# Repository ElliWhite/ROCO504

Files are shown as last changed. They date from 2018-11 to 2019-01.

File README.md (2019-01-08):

# ROCO504: Advanced Robot Design
## Active Robot Fall-Absorption Mechanism
### Mason Carter, Luka Danilovic, Elliott White

This is a repository to hold all the files for the ROCO504 project.

#### Requisites
The NUCLEO-F746ZG code needs to be loaded into https://os.mbed.com/ online compiler for it to work. 

mbed-os.lib revision 4928:e1bea44 also needs to be added to the project. 

### Project Assignment
For the assignment the group will need to design, implement and evaluate an advanced robot
design. Typical skills to be acquired/demonstrated include the use of CAD, FEA, 3D printing,
materials, mechanisms, robot programming and structural analysis. The project will enable the participents to
study, implement and test various aspects of robotics, including soft and exotic materials, novel
actuation principles, 3D-printable structures, and the interaction of a robot with its environment. 
A budget of £70 for the project is given.

### Abstract
The purpose of this research project was to design and build a prototype robot to serve as a proof of concept for a Active Robot Fall-Absorption Mechanism. Large robots with a small foot-base will inevitably fall over, so we have designed a mechanism to dampen the fall of a robot and reduce any damage caused to it from the fall. Upon successful completion of the building of the mechanism and conducting tests, our findings indicate that with slight improvements, originally not possible due to budget constraints, this project would yield a beneficial mechanism capable of performing its task of dampening a fall of a much larger robot.

### Introduction
As the trend of Robotics leans towards creating taller robots, more researchers are struggling with the task of trying to keep a robot with a small foot-base upright. The robot will, inevitably, fall over. This can cause massive damage to the robot, mostly consisting of mechanical damage to the links between joints, or servo damage. Until fall prevention becomes more effective, a simpler fall-damage-reduction system would be incredibly useful. 

We propose to design and create a robotic body and leg, for the provided budget of £70.00. The main body will consist of agonist-antagonist actuators and can detect when a robot has fallen past its self-balancing point. The leg will then reach out and use artificial tendons to reduce the falling speed of the body. This can be comparable to how a human might brace themselves when falling. The artificial tendons are used to store potential spring energy. 

### Design
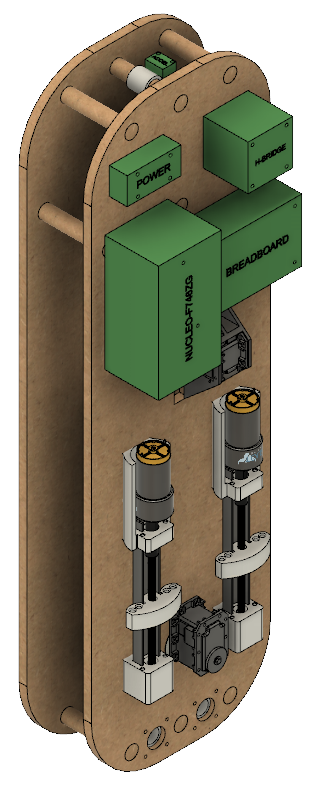
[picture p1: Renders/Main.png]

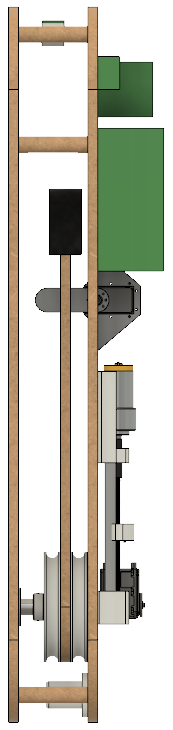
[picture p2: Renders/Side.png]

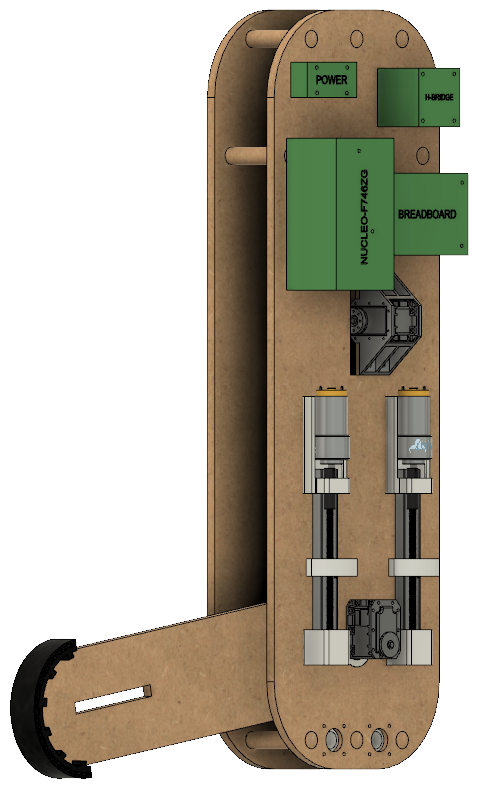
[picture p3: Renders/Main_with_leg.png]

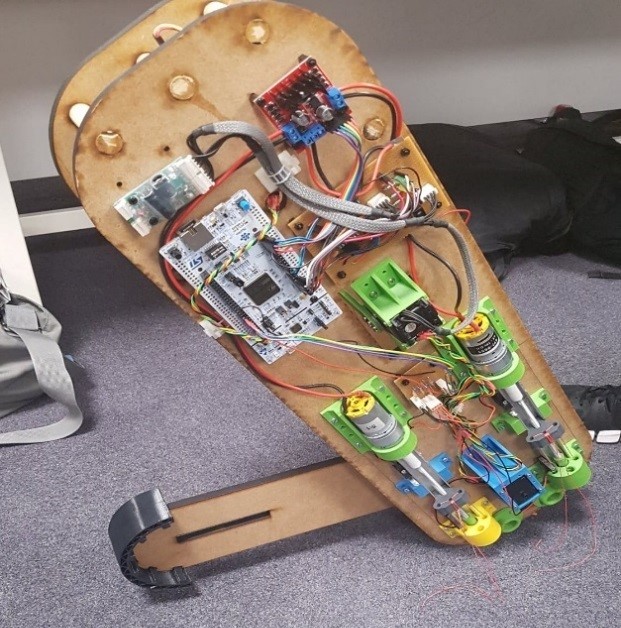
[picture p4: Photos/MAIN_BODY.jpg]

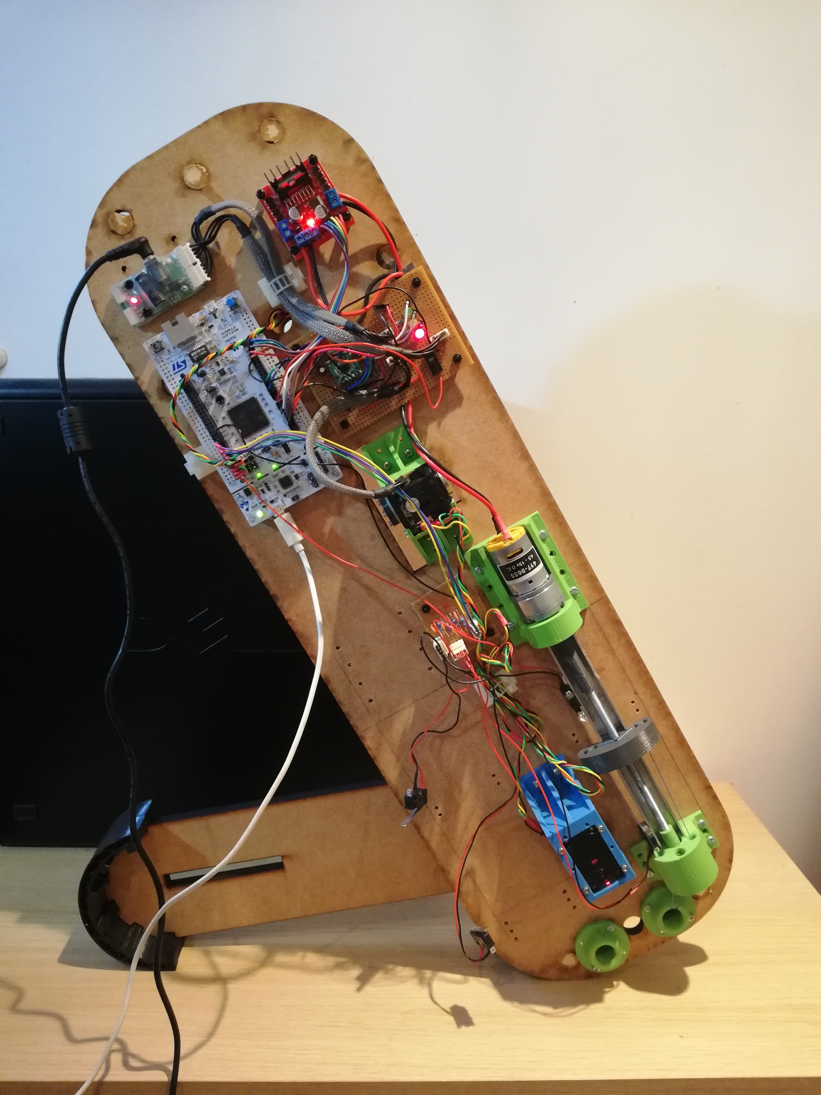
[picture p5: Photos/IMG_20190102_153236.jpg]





### Conclusion
Video: https://youtu.be/zlB8UxlkwFY

We have built a platform that, with more work, will be capable of demonstrating the use of agonist-antagonist joints and artificial soft tendons to absorb a fall of a robot. The software algorithms that are in place are capable of successfully executing a fall-reduction system, but it is the hardware that causes limitations. The motors do not have enough torque to slowly lower the body down to the floor, nor have a high enough RPM to tension the leg to a high enough degree before the body reaches the floor. 

The biggest improvement to be made would be changing the DC motors to a more powerful version. This would enable a faster actuation of the linear actuators and also allow the actuators to move when under heavy load and not stall. This change would also require a change to the motor driver IC to a part that would be able to handle the higher current.
A new pulley would have to be designed to stop the nylon-to-Fila-Flex adapter from slipping off during leg deployment. This would be a simple redesign and the modification that would need to be made would be to widen the pulley to the extent that there is no space between the pulley and the body for the adapter to fall into.

Another modification would be the leg pre-tensioning and release mechanism. The new control algorithm and mechanism would pre-tension both tendons at the same time regardless of which direction the body is falling. Then, upon detecting a fall, the mechanism would release one tendon and tighten the other one further. This would allow a quicker response time as there is no wait for one tendon to be tensioned and the other one un-tensioned during the time before a fall is detected.

The budget of £70 was a major limiting factor, and with a larger budget and with the previously-mentioned changes made, we believe the system would be successful in its ability to absorb the impact from a fall and not allow any damage to be caused to the robot it is attached to.

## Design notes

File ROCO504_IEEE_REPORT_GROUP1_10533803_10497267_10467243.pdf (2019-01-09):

# Active Robot Fall-Absorption Mechanism

Mason Carter
School of Computing, Electronics and Mathematics
University of Plymouth
Plymouth, UK
mason.carter@students.plymouth.ac.uk

Luka Danilović
School of Computing, Electronics and Mathematics
University of Plymouth
Plymouth, UK
luka.danilovic@students.plymouth.ac.uk

Elliott White
School of Computing, Electronics and Mathematics
University of Plymouth
Plymouth, UK
elliott.white@students.plymouth.ac.uk

Abstract – The purpose of this research project was to design and build a prototype robot to serve as a proof of concept for an Active Robot Fall-Absorption Mechanism. Large robots with a small foot-base will inevitably fall over, so we have designed a mechanism to dampen the fall of a robot and reduce any damage caused to it from the fall. Upon successful completion of the building of the mechanism and conducting tests, our findings indicate that with slight improvements, originally not possible due to budget constraints, this project would yield a beneficial mechanism capable of performing its task of dampening a fall of a much larger robot.

Keywords – Fall absorption, agonist-antagonist, variable stiffness, soft robot.

I. INTRODUCTION
As the trend of Robotics leans towards creating taller robots, more researchers are struggling with the task of trying to keep a robot with a small foot-base upright. The robot will, inevitably, fall over. This can cause massive damage to the robot, mostly consisting of mechanical damage to the links between joints, or servo damage. Until fall prevention becomes more effective, a simpler fall-damage-reduction system would be incredibly useful.

We propose to design and create a robotic body and leg, for the provided budget of £70.00. The main body will consist of agonist-antagonist actuators and can detect when a robot has fallen past its self-balancing point. A leg will then reach out and use artificial tendons to reduce the falling speed of the body. This can be comparable to how a human might brace themselves when falling. The artificial tendons are used to store potential spring energy.

II. DESIGN

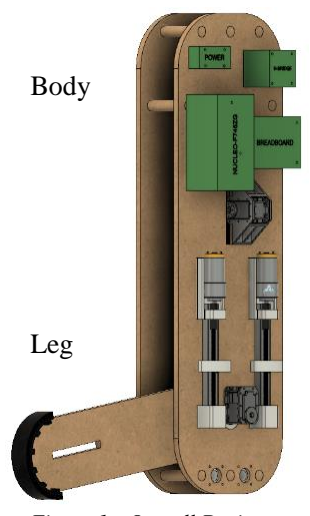
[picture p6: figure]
Body; Leg

Figure 1 - Overall Design

A. Mathematical Theory
Before the release of the leg, the falling motion of a robot is the same as that of an inverted pendulum. The model of an inverted pendulum and its corresponding equations [1] can be used to calculate the angular acceleration and thus the fall time of the robot. The calculations assume no friction or other resistance to movement, and any acceleration is due to gravity.
τ = mgl sin θ | (1)

τ = Iθ̈= ml

2 × θ̈ | (2)

ml

2θ̈= mgl sin θ | (3)

θ̈=

g
l
sin θ | (4)

t = √
(90 − θ)
θ̈
⁄ | (5)

Where:
- τ is the net torque around the pivot point.
- m is the mass of the body.
- g is the acceleration due to gravity.
- l is the length of the mass from the pivot point.
- θ is the angular displacement from the equilibrium.
- I is the moment of inertia of point mass.
- θ̈is the angular acceleration of the pendulum.
- t is the time to fall from the current angular displacement to perpendicular with the angle of equilibrium.

The time to fall can then be used to find the ‘activation window’, or the amount of time the leg will have to activate and contact the ground before the body is past its maximum angle. The maximum angle is an angle from the equilibrium that we feel the body could not be saved from with the use of the leg.

TA = √
(90 − θ1

)
θ̈
1

⁄ − √
(90 − θ2

)
θ̈
2
⁄ | (6)

Where TA is the activation window, θ1 is the current
angular displacement, θ2

is the maximum angle, θ̈
1

is the
angular acceleration for the current angular displacement, and θ̈
2

is the angular acceleration for the maximum angle.

With the calculation of the activation window, we can find the torque required to accelerate the leg quickly enough that it will contact the ground first.

θ̈
LEG =

θLEG
TA

2

(7)

θARM is the angle from its stored position (parallel to the body), and can be calculated using the following equation.

θLEG = θ − 90− sin⁻¹

l1 sin(90−θ)
l2

(8)

Where θ is the angular displacement of the body from equilibrium, l1
is the distance of the leg pivot to the base of the body, and l2
is the length of the leg.

Given the angular displacement, we can then calculate the angular acceleration required to activate and contact the ground in the activation window (Results for all cases in Appendix 1).

τLEG = mLEG × lLEG

2 × θ̈
LEG | (9)

Where τLEG is the torque around the leg’s pivot point, mLEG is the mass of the leg, lLEG is the distance of the legs centre of mass to the leg pivot point, and θ̈
LEG is the angular
acceleration of the leg required for the activation window.

As we can only make a rough estimation as to the dimensions of the body and leg, upper, middle and lower estimations were evaluated. 20° and 70° were chosen for the minimum and maximum activation angles. The torque required to activate by the maximum angle was calculated for each degree between the minimum and maximum angle, though not including the maximum.
This produced 50 results for each estimation, and with there being 5 unknown variables that can be estimated(l, l1 ,
l2

, lLEG, mLEG), the number of results quickly increases. To more quickly process and evaluate these results, a MATLAB script was written to carry out the calculations and output a ‘.csv’ file which can then be opened in Microsoft Excel. The variables were evaluated for values between 0.1 and 0.5, at intervals of 0.1. With the maximum angle set at 70°, we decided that the latest the leg should be able to activate would be at 45°, since the torque required for the leg to activate and contact the ground after 45° but before 70° would be incredibly large. Calculations showed that the torque required after this point could be up to 50000 Nm. With these variables, the minimum torque required would be 0.04 Nm and the maximum would be 93.7 Nm.

B. CAD and Mechanical Design
1) Design Overview
The body consist of two 9mm thick MDF, laser cut plates, (see Figure 1 for full CAD overview). The front plate, called the spine, serves as the attachment point for the PCBs, wiring, left and right tendon tensioning mechanisms, tendon guides, leg encoder Dynamixel servo, leg release

Dynamixel servo and the metal leg axle with bearing assembly. The Dynamixel servos were not included in the project budget as these were available for use when the project was undertaken. The second plate at the back serves to add depth to the body and provide additional structural support to the leg axle. This plate is attached to the spine via 7 dowels. The body has rounded corners at the bottom face so that area in contact with the ground will remain constant during the tipping of the body. Lighter components such as the PCBs have been mounted towards the top of the body with heavier components being pushed towards the base as much as the design permits. An accelerometer has been mounted at the top in line with the middle of the leg and oriented along the pivoting axis. (STL files for all components are available in Appendix 2).

2) Leg Design
The Leg consist of a single link as a multiple link configuration was found to be too complicated for a negligible improvement in performance. The leg can deploy along the tipping axis in forwards or backwards directions and is slightly raised from the base of the body to allow for deployment angle greater than 90o
. The base of the leg
contains a series of holes for attaching the tendons as well as two pullies of constant diameter around which the tendons wrap to ensure a constant force is exerted on the leg regardless of its orientation. The tendons are kept from tangling by using guide tubes to ensure alignment between the pulleys and the tensioning mechanism. The top of the leg is outfitted with a circular profile rubber “foot” to constantly provide same area of contact with the ground. Furthermore, the foot is 3D printed using NinjaFlex filament which creates a soft model. The foot also includes a self-resettable crumple zone to provide an additional element of compliance during a fall and to minimise the impact force of the leg. The leg also has positional feedback provided by the bottom Dynamixel (with gears removed to enable 360o
free rotation), while the leg release is controlled by a lever attached to a second Dynamixel positioned near the top of the leg. The whole leg is supported by a metal axle with bearings on both ends in the spine and back plate. This provides a stable axis of rotation and eliminates wobbling even in the cases of the hard impacts of the leg against the floor.

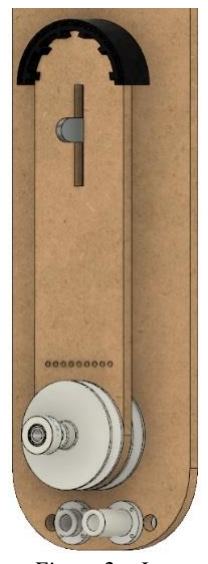
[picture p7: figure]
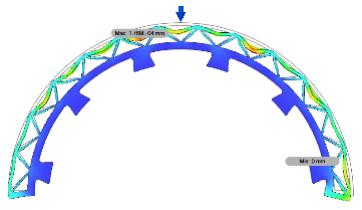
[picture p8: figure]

Figure 2 – Leg Figure 3 - Foot deformation under 500N Load

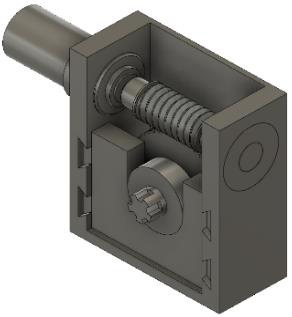
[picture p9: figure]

Figure 4 - Worm & Gear gearbox

3) Tensioning Mechanism Design
During the preliminary calculations phase, a goal was imposed on the tensioning mechanism so that it will be capable of 150mm of linear pull in 1 second. To achieve this a 12V DC motor was selected for its speed and torque. A 1974RPM (≈2000RPM) output was chosen for convenience with the highest torque option for the gearbox being selected at 1284gcm. To translate the motor rotation into linear movement of the tendons, a winding pulley was used with worm & gear gearbox (Figure 4) to make the tensioning mechanism non back-drivable. Therefore, the size of the pulley was calculated according to equation 10.

d =

60LN
πR

; {

d = Pulley Diameter
L = Linear Pull per Second N = Gear box ratio 1: N
R = RPM of tℎe Motor

(10)

After prototyping, it was determined that the best gearboxes worked with a ratio between 1:40 & 1:60. Therefore, number of teeth picked for the worm wheel is 48 to give a pulley diameter of 70mm. This in turn translates to a circumference of 220mm (>150mm). However, once the whole mechanism was assembled and run, there were friction problems which would cause failure of parts over prolonged use. Due to our budget constraints, we were unable to find a suitable prebuilt metal alternative and have therefore changed the design of the tensioning mechanism. Following the preliminary design review, a decision was taken to use a screw mechanism based on 3D printer Z-axis movement (Figure 5). A prototype was built, and a test was conducted to assess the viability of the mechanism. After a successful test, a full-scale device was built with support for 1.75mm and 2.5mm Fila-Flex tendon thickness. Minor

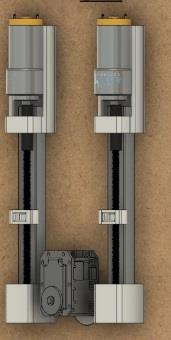
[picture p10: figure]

Figure 5 - Tensioning Mechanism Final Design

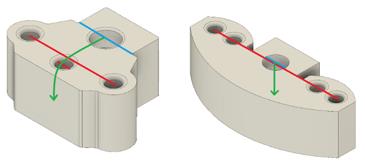
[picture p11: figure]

Figure 6 - Old and New Runners with respective Angular Moments

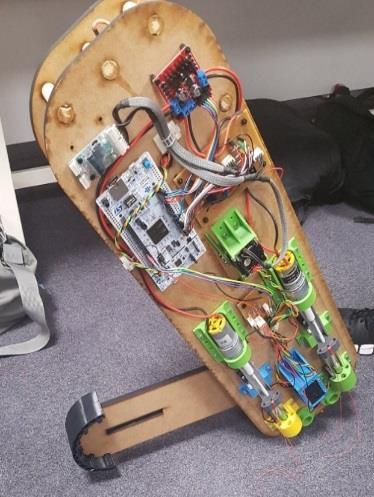
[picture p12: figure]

Figure 7 - Assembled Mechanism

changes were made to the shape of the tendon attachment points on the linear runner to reduce the angular moment on the runner and screw rod (see Figure 6) and therefore maximise the motor torque utilisation. This was done by aligning the mounting holes with the plane of the degree of freedom to achieve perpendicular force. The final design, when assembled, can be seen in Figure 7.

4) Tendon Design
The original tendon design was heavily inspired by the GummiArm [2]. Using a single strand of 2.85mm Fila-Flex and wrapping a string of nylon with ≈ 5mm spacing, we were able to test the tensioning mechanism but discovered that the strength of the nylon was not enough. Therefore, we switched to 1.75mm Fila-Flex and created a three-strand braid with 4th and 5th strands of nylon woven through. However, after conducting tensile testing on all configurations we realised that braid did not provide significant improvement over a straight three strand tendon, although it did add to the manufacturing complexity. To mitigate this, we switched back to a single strand of 2.85mm thick Fila-Flex. The final design that was chosen consists of double nylon strands connected to the runners on one end and via an adapter a strand of 2.85mm thick Fila-Flex on the other. Thicker filament was chosen for its strength and deformation properties. Fila-Flex then wraps around the

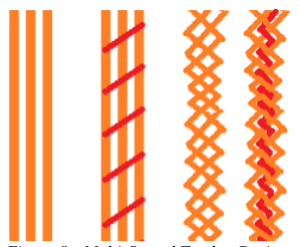
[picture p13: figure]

Figure 8 - Multi-Strand Tendon Designs pulleys and connects to the leg. As seen in Figure 9, there is a secondary nylon strand present in parallel with the Fila-Flex to take the force once the Fila-Flex is stretched passed the designated limit.

Figure 9 – Compound Tendon Diagram

C. Electronics & Software Design
The whole system is built around a STM32F746ZG MCU which sits upon a NUCLEO-F746ZG development board, produced by STMicroelectronics. The motor driver selected is a Dual H-Bridge Module produced by Hobby Components, which contains a L298N produced by STMicroelectronics. The L298N can provide up to 2A continuous per channel, or 2.5A repetitive (80% on, -20% off). This motor driver module is connected to two RS PRO brushed DC geared motor. These DC motors have a stall current of 2.26A. The L298N can handle the stall current of these motors, but it should be noted that if other, more powerful motors were to be used, then a different motor driver would need to be chosen. The six-axis inertial measurement unit selected is an inexpensive MPU-6050, produced by TDK InvenSense, and comprises of a gyroscope and an accelerometer. This IMU sits on a breakout board produced by SODIAL, the GY-521. Communication to the sensor is achieved through I2C. Dynamixel servos have been used in the design. The two Dynamixel servos are RX-28s, and these require the RS-485 communication protocol. Because of this, a MAX3088 RS-485 transceiver IC has been used in line with a MAX3378 voltage-level shifter and are connected to a UART port on the NUCLEO board with a baud rate of 57600. The servos can be connected in a daisy chain-like manner. Microswitches have been used on the linear actuators to provide positional feedback of the linear runners when they reach their limit. LEDs have also been used for visual debugging and system information. An outline of the system can be seen in Figure 10.

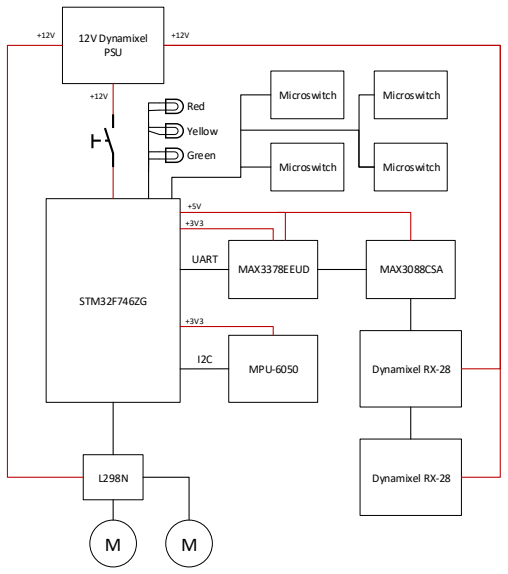
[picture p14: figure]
STM32F746ZG; 12V Dynamixel PSU; MPU-6050; Dynamixel RX-28; Red; Green; Yellow; MAX3378EEUD; MAX3088CSA; Microswitch; UART

Figure 10 - Electronics System Outline

One of the Dynamixel RX-28s has been used as an encoder to provide positional feedback of the leg. To achieve this, the gears have been removed so the servo is free to spin. Communications between the RX-28s and the NUCLEO board occur by sending and receiving digital packets. A library on Mbed had been provided [3] to enable communications with the servos. However, this library had to be modified to get it working with the RX-28s. Timings in the existing library had been incorrect, so the microcontroller would completely miss the returning status packet from the servos. If the microcontroller tried to communicate with a servo that wasn’t in the servo chain, then the code would enter an infinite wait. This has been changed to include a timeout if a status packet isn’t received within 5000 checks of the serial input buffer. A new function had been implemented to find the servo ID numbers of the servos in the servo chain. This means that the servos could be switched out with other RX-28s, and the code would still work. The baud rates of the Dynamixel servos can be changed by modifying data in the registers on the on-board EEPROM. Because of this, some of the servos had different baud rates to each other at the start of the project. An algorithm was implemented to quickly adjust the baud rates of the servos in the chain by utilising the “broadcast” command, which sends an instruction to all the servos on the chain. This algorithm ensured that all servos in the chain had the same baud rate before the rest of the code ran. Tests were done to identify the servos in the chain and to move the servos to different positions. Reading back the positional data was also done to ensure that the communications with the servos were established correctly.

To test and use the MPU-6050, an existing header and main file had been used that was provided on Mbed [4]. These files provided all the functionality to read acceleration and angular data. The algorithm uses Quaternions to avoid gimble lock in the gyroscope. This is especially useful in this scenario as the robot will approach +/- 90 degrees in one axis. The Quaternions are then converted to Euler angles using the conversion equations 11-13.
φ (yaw) = arctan (

2(ab+cd)
a²−b

2−c

2−d²

| | | | ) | | (11)
θ (pitcℎ) = −arcsin(2(bd − ac)) | (12)

ψ (roll) = arctan (

2(ad+bc)
| | | a²+b 2−c | 2−d²
| | | | ) | | (13)

To test the IMU, continual data was streamed to a serial monitor to observe the angular data of the device. The device was then rotated around its separate axis and the measured data was compared to the real angles of the device.

All the software has been written in C++ using ARM’s Mbed OS, which is a platform and operating system for
devices | based | on | the | 32-bit | ARM | Cortex-M
microcontrollers. This has enabled rapid code development and fast deployment. The algorithms used focus heavily on gyroscopic and accelerometer data as it is this data that

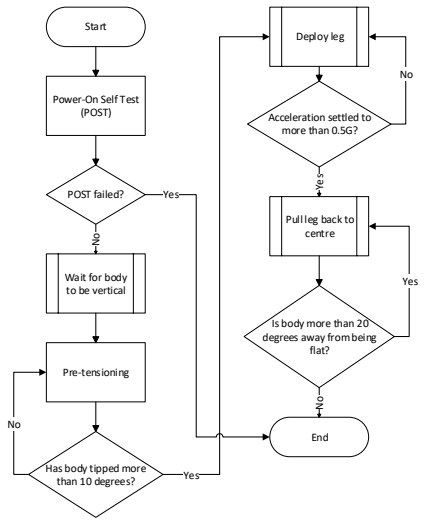
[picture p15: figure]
Start; Power-On Self Test (POST); POST failed?; Wait for body to be vertical; Pre-tensioning; Has body tipped more than 10 degrees?; Acceleration settled to more than 0.5G?; Deploy leg; Pull leg back to centre; Is body more than 20 degrees away from being flat?; End; No Yes; Yes

Figure 11 - Code Algorithm Outline

provides all the information about the given state of the body. Data from the IMU is gathered asynchronously as it is not critical to observe the physical state of the body at a given rate. An outline of the algorithm used for this project can be seen in Figure 11.
As seen in Figure 11, the algorithm begins by running a POST test. This ensures that all components are working and that communications with the Dynamixels are established. The pre-tensioning function tensions the tendons on the leg before the body has begun to fall. This is done by detecting which direction the body is starting to tip, and subsequently pull on the relevant tendons. If the body is tipped more than 10 degrees, this is classed as a ‘fall’ and the leg is deployed in the correct direction. The acceleration data is then monitored until it settles. This shows that the body has stopped falling and is resting on the leg. The leg is then pulled back towards the centre of the body using positional data from the Dynamixel on the shaft of the leg to monitor its progress.

III. EXPERIMENTS

A. Tensile Testing
In order to pretension the agonist-antagonist joints, an elastic material would be used as a tendon. The kinetic energy from the pre-tensioning would be stored in the tendon to be released as needed. Flexible 3D printing filament (FilaFlex [5]) would be used, both because of cost and its elasticity at break of 665%.
Three strands of the filament would be used, because the pre-tensioning forces had been estimated to be too much for a single strand, and to also provide a built in redundancy in the case of a strand snapping. As with rope, it was thought that the tensile strength of the material could be increased by braiding the strands, so test samples were produced for both un-braided and braided. However, while an elastic material is needed, the elasticity of the filament seemed too high, so a compound tendon using Nylon was considered. Test samples for unbraided with nylon and braided with nylon were also produced for tensile testing. Two test samples for each configuration of the strands were tested for their tensile strength, but because of inadequate clamping

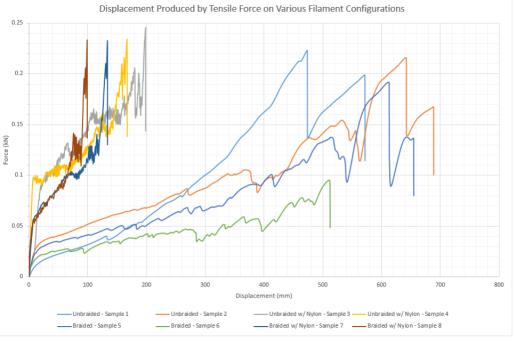
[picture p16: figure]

Figure 12 - Copy of the Tensile Testing Results Graph

methods the samples tended to slip through the clamping mechanism. Appendix 3 contains the results of the testing. The graph in Figure 12 and in Appendix 3 shows that while the samples with and without Nylon are clearly separated, braiding has no effect on the tensile strength of the material.

B. Fall Testing
In order to be able to correctly use the accelerometer and gyroscopic data, the body needed to be repeatedly pushed over and the data recorded. This allowed the system to know the state of the body based on the data. The tendons were configured in a way that would allow the body to rest at an angle with all the weight resting on the tendon. The right motor was spun until the linear actuator had pulled a substantial amount on the tendon. This can be seen in Figure
13. The body was then up-righted and pushed over with a small amount of force. The acceleration in the x-axis was monitored and plotted through a serial connection to a MatLab script. This plot can be seen in Figure 14. At sample 150, the body starts to fall. At 380, the Fila-Flex starts to dampen the fall and slow the body down, and at sample 420 the nylon takes over which causes the large jump in acceleration. As the body settles to its resting position, so does the acceleration which settles at 0.9G. It does not settle at 0G as the accelerometer is measuring the acceleration due to Earth’s gravity. Initially, a value of 0 will be measured, but as the body tips over more, the value will increase until it reaches 1G when the body is perpendicular to the floor. This data has helped shape the control algorithm (Appendix 4). If the acceleration has settled to a high value, then it can be known that the body has stopped moving and is resting on the leg. The leg can then start to be pulled back towards the body and lower the body down towards the ground. It was decided that if the acceleration settles to a value above 0.5G, then the body has successfully fallen and is resting on the leg (Appendix 5 - Video).

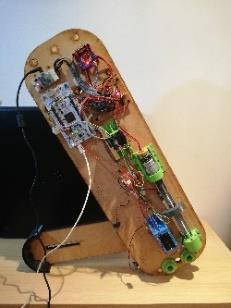
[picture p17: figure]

Figure 13 - Body Resting on Leg

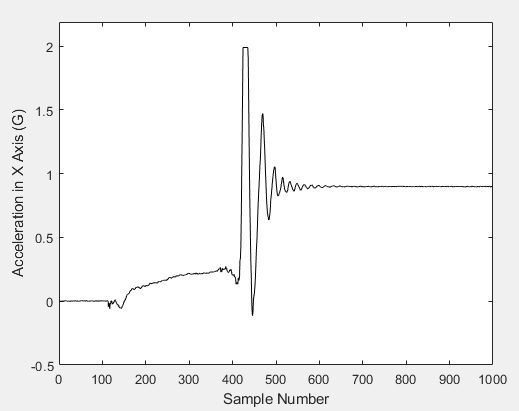
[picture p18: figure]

Figure 14 - Graph Showing Change in Acceleration in X-Axis

C. Lowering Body Testing
The next experiment was testing to see if the body could be lowered slowly to the ground once it had rested on the leg. The body was placed at an angle with all of the strain on the tendons, and then the right motor was spun in such a way that would pull the leg into the body and allow the body to reach the floor. It was found that the motor would stall and not have enough torque to move the linear actuator. The body would not be able to be lowered down to the floor. The force of the tendons pulling on the linear runner was causing too much friction between the nut and the threaded rod, stopping the motor from spinning.
D. General Testing
Once the body was built there was a lot of general testing of tipping the body and pushing it over, and then observing how the control algorithm was performing. During this testing, it was found that the tendons would never tension enough when the body was falling. The RPM of the motors were not high enough to move the linear actuator far enough in the time given for the body to fall over.
We also found that when the leg sprung out and the body tipped, the tendon would become displaced from the pulley (see Figure 15). This resulted in a much looser tendon as it was not stretched around the pulley. This, coupled with the fact that linear actuator would not move far enough, meant that the tendon would never be taught enough to have any effect on dampening the fall of the body.

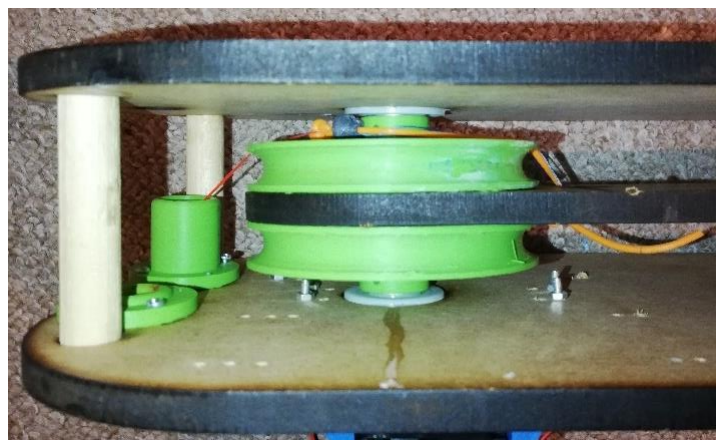
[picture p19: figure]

Figure 15 - Tendon Slipped off Pulley

IV. CONCLUSION
We have built a platform that, with more work, will be capable of demonstrating the use of agonist-antagonist joints and artificial soft tendons to absorb a fall of a robot. The software algorithms that are in place are capable of successfully executing a fall-reduction system, but it is the hardware that causes limitations. The motors do not have enough torque to slowly lower the body down to the floor, nor have a high enough RPM to tension the leg to a high enough degree before the body reaches the floor. The biggest improvement to be made would be changing the DC motors to a more powerful version. This would enable a faster actuation of the linear actuators and allow the actuators to move when under heavy load and not stall. This change would also require a change to the motor driver IC to a part that would be able to handle the higher current. A new pulley would have to be designed to stop the nylon-to-Fila-Flex adapter from slipping off during leg deployment. This would be a simple redesign and the modification that would need to be made would be to widen the pulley to the extent that there is no space between the pulley and the body for the adapter to fall into. Another modification would be the leg pre-tensioning and release mechanism. The new control algorithm and mechanism would pre-tension both tendons at the same time regardless of which direction the body is falling. Then, upon detecting a fall, the mechanism would release one tendon and tighten the other one further. This would allow a quicker response time as there is no wait for one tendon to be tensioned and the other one un-tensioned during the time before a fall is detected. The budget of £70.00 was a major limiting factor, and with a larger budget and with the previously-mentioned changes made, we believe the system would be successful in its ability to absorb the impact from a fall and not allow any damage to be caused to the robot it is attached to.

APPENDIX
Appendix 1 – Force Calculations https://github.com/ElliWhite/ROCO504/tree/master/Force %20Calculations (https://github.com/ElliWhite/ROCO504/tree/master/Force%20Calculations)

Appendix 2- STL Files
https://github.com/ElliWhite/ROCO504-Advanced-Robot-Design-Project/tree/master/STL%20Files (https://github.com/ElliWhite/ROCO504-Advanced-Robot-Design-Project/tree/master/STL%20Files)

Appendix 3 – Tensile Testing Data and Results
(Graph available in “Displacement vs. Force” worksheet). https://liveplymouthac-my.sharepoint.com/:x:/r/personal/elliott_white_students_plymouth_ac_uk/_layouts/15/Doc.aspx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 56e5c-52d3-4ef5-bb82-
3eb3c2f34c49%7D&action=default (https://liveplymouthac-my.sharepoint.com/:x:/r/personal/elliott_white_students_plymouth_ac_uk/_layouts/15/Doc.aspx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)

Appendix 4 – GitHub Repository
(ReadMe available) https://github.com/ROCO504/2018-Group1 (https://github.com/ROCO504/2018-Group1)
Populated repository can be found at: https://github.com/elliwhite/roco504

Appendix 5 – Video demonstrating the Project https://youtu.be/zlB8UxlkwFY

ACKNOWLEDGMENT
This research was supported by Martin Stoelen from the University of Plymouth CRNS. We thank our colleagues from University of Plymouth Robotics Department who provided insight and expertise that greatly assisted the research, although they may not agree with all of the interpretations/conclusions of this paper.
V. REFERENCES
[1] Wikipedia, “Inverted Pendulum,” 15 June 2018.
[Online]. | Available:
https://en.wikipedia.org/wiki/Inverted_pendulum. [Accessed October 2018].
[2] M. Stoelen, “GummiArm,” 2017. [Online]. Available: https://mstoelen.github.io/GummiArm/. [Accessed November 2018].
[3] D. Gongora, “Dynamixel,” 25 October 2015.
[Online]. | Available:
https://os.mbed.com/users/dmgongora/code/Dynamixel/. [Accessed October 2018].
[4] K. Winer, “MPU6050IMU,” 29 June 2014.
[Online]. | Available:
https://os.mbed.com/users/onehorse/code/MPU6050IMU/.
[5] | Recreus, | “FilaFlex | Original | 82A,” | 2017.
[Online]. | Available:
https://recreus.com/img/pdf/FILAFLEX%2082A%20TECHNICAL%20SHEET%20&%20MSDS%2 02017.pdf. [Accessed October 2018].

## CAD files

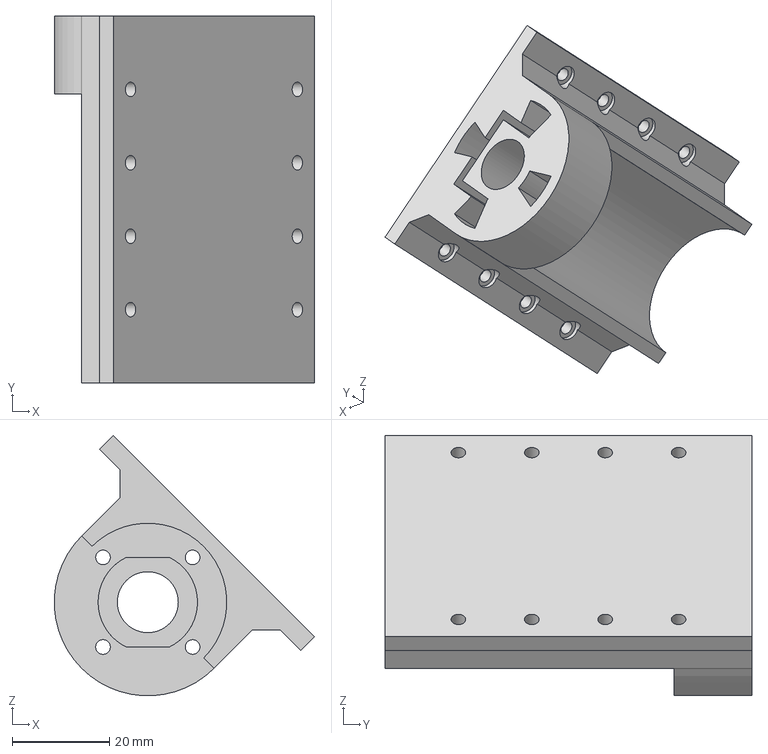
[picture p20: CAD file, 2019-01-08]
STEP Files/Motor Mount v5.step
53.4 x 75.3 x 53.4 mm

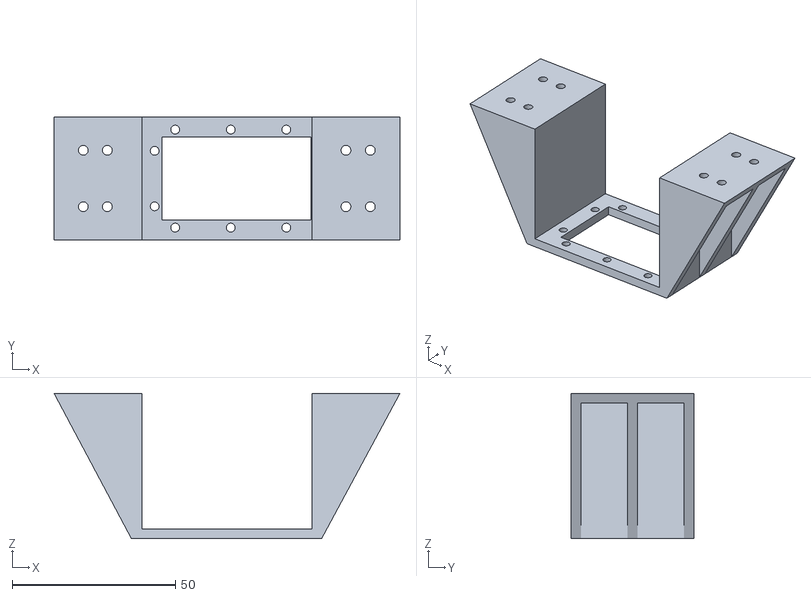
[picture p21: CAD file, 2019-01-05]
STL Files/Bottom Dynamixel Bracket v5.stl
105.9 x 37.5 x 44.5

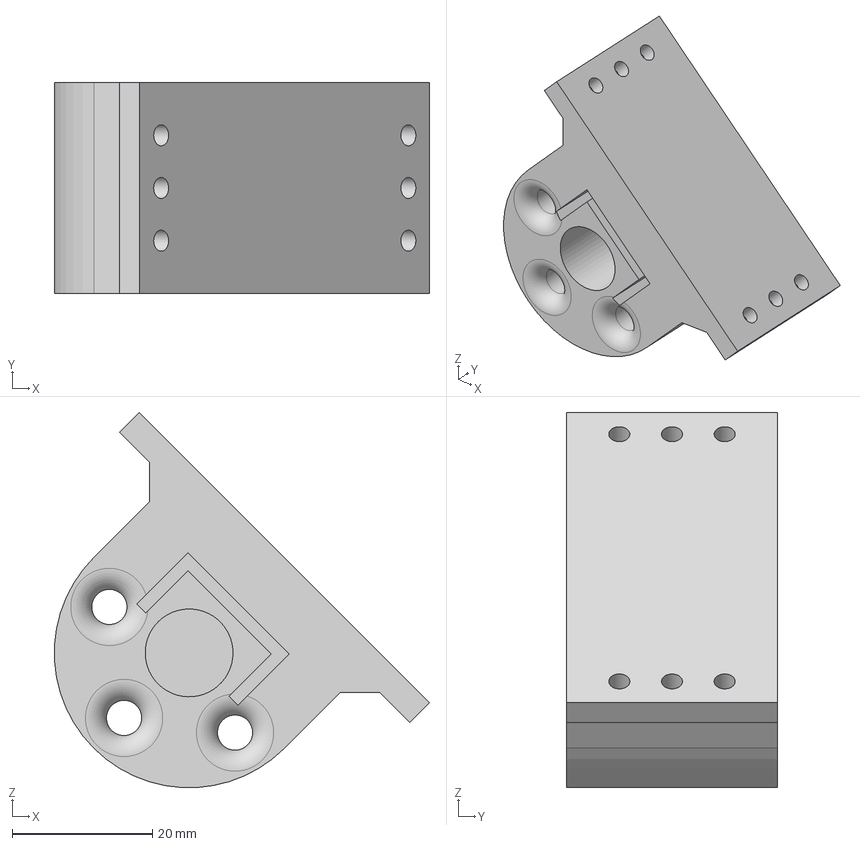
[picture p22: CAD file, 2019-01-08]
STEP Files/Runner End v5.step
53.4 x 30.0 x 53.4 mm

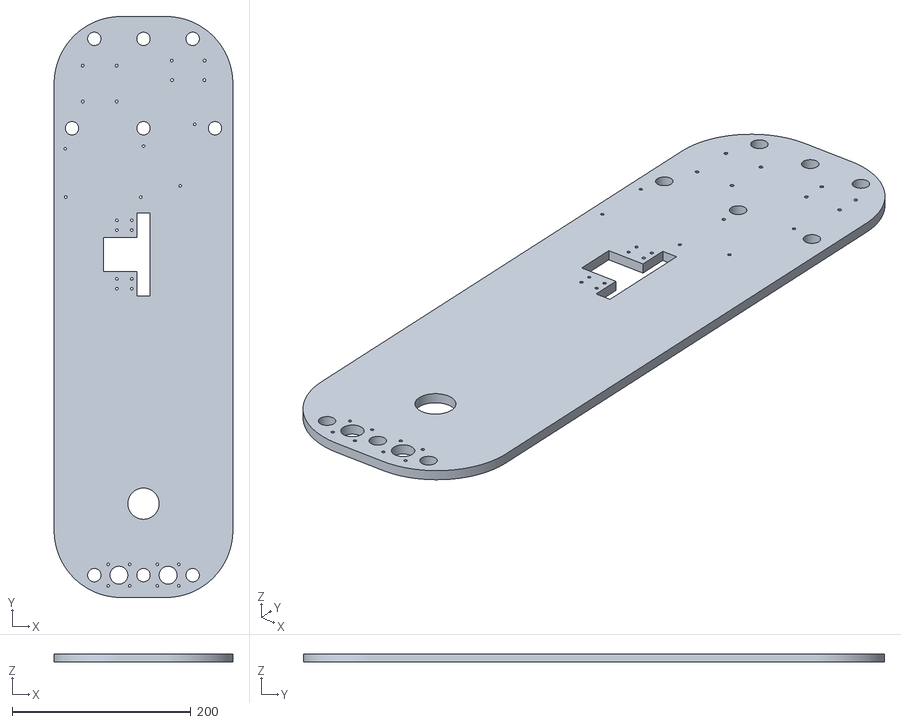
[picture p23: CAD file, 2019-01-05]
STL Files/Spine v6.stl
200.0 x 650.0 x 9.00

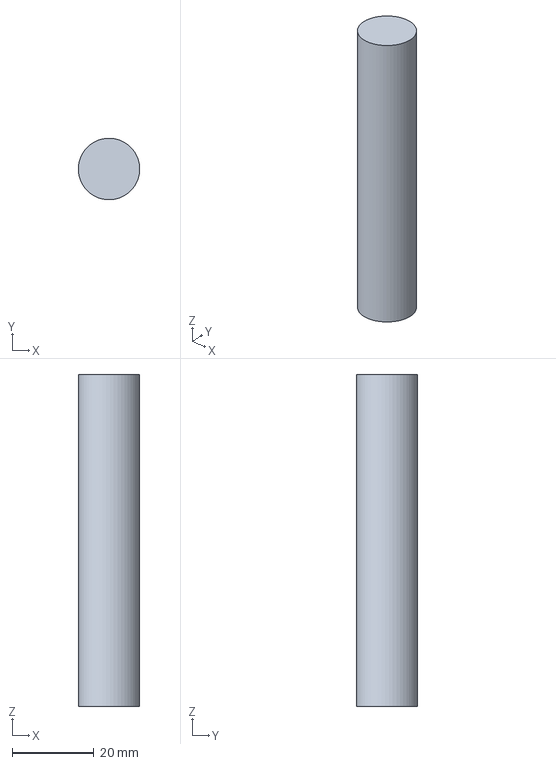
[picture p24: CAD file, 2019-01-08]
STEP Files/Dowel v11.step
15.0 x 15.0 x 81.0 mm

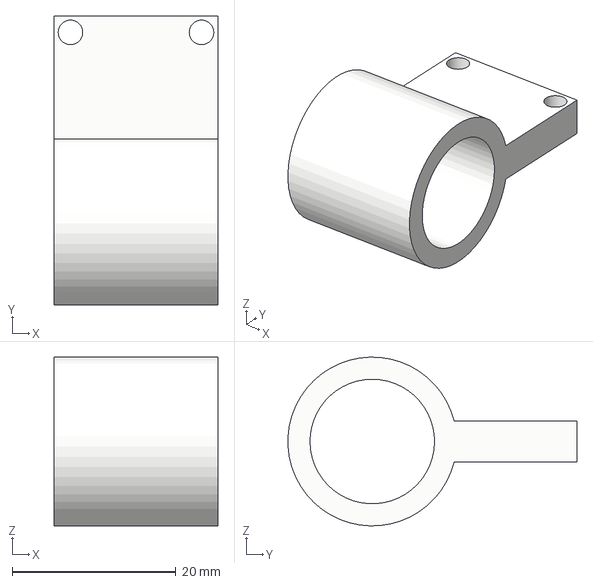
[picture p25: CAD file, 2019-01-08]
STEP Files/Acc Bracket v1.step
20.0 x 35.3 x 20.6 mm

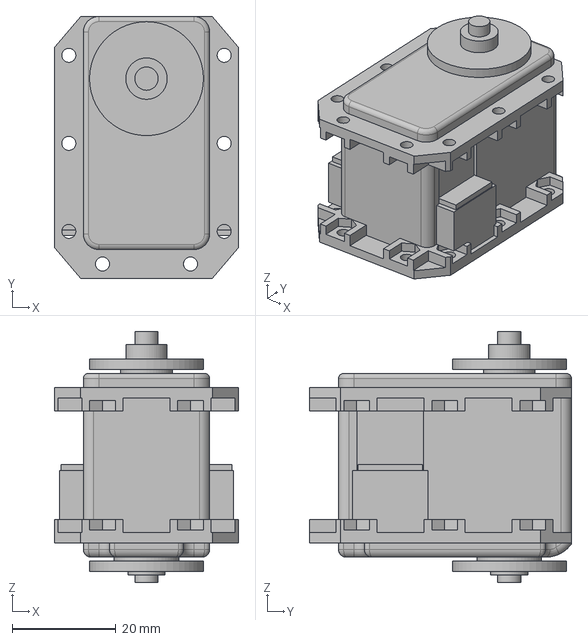
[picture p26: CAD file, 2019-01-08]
STEP Files/Dynamixel RX28 Representation v1.step
35.6 x 50.6 x 48.5 mm

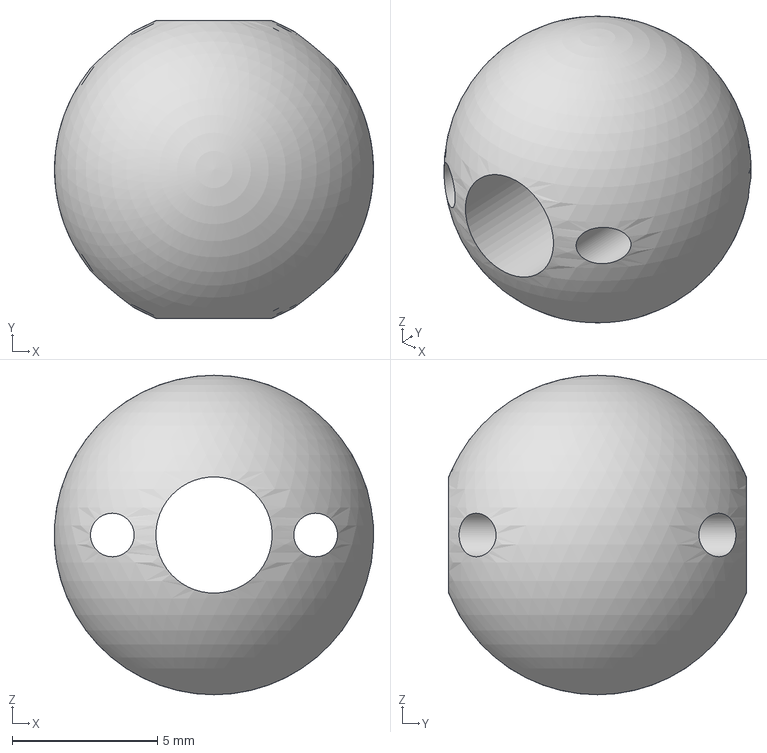
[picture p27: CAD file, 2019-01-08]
STEP Files/Nylon To Flex Adapter v4.step
11.0 x 10.2 x 11.0 mm

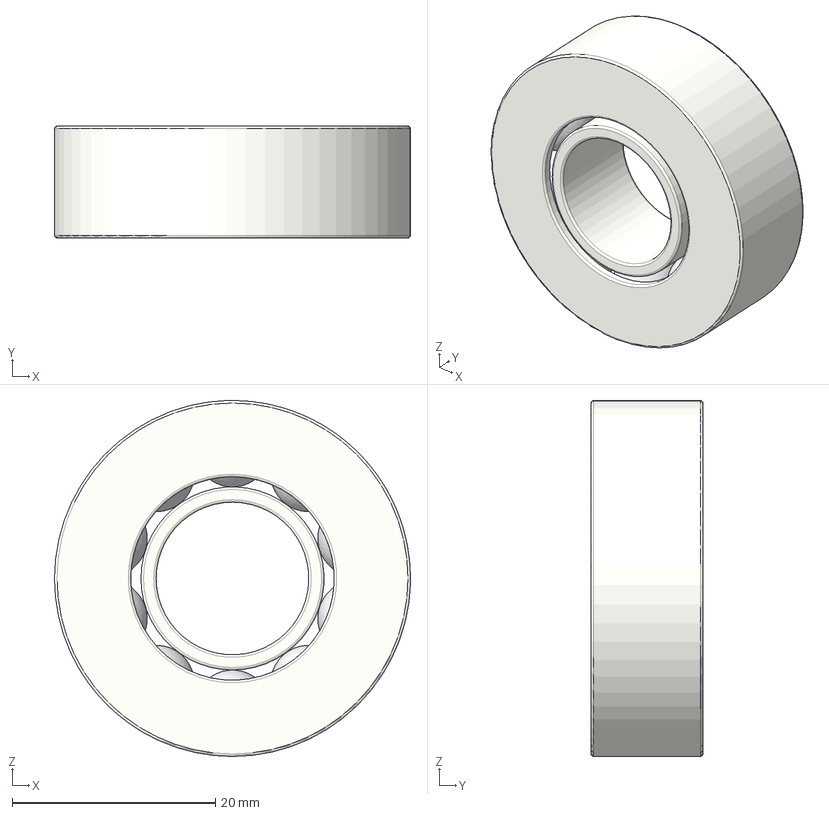
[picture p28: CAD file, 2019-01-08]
STEP Files/Bearing v3.step
35.0 x 11.0 x 35.0 mm
Outer Shell
Inner Shell
Ball Bearing

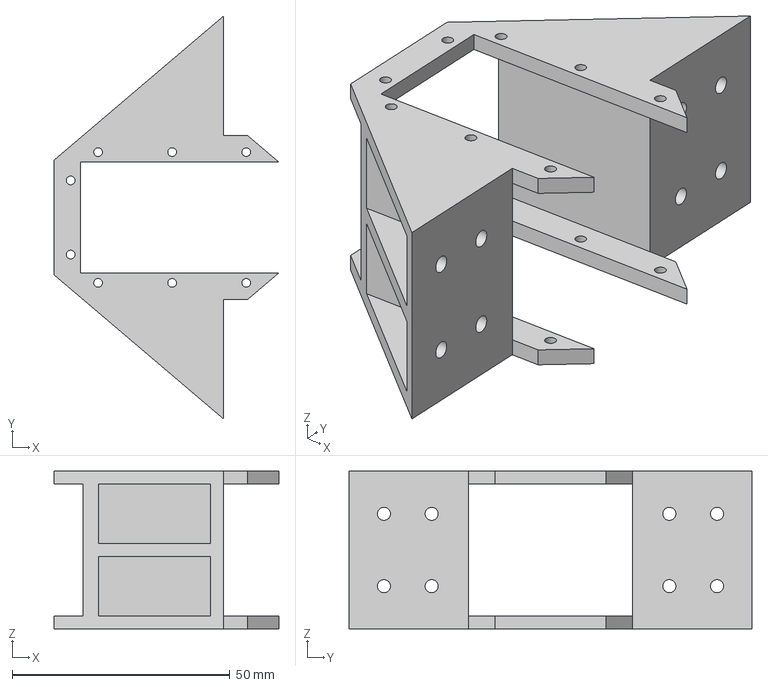
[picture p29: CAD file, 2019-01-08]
STEP Files/Top Dynamixel Bracket v4.step
51.6 x 92.5 x 36.2 mm

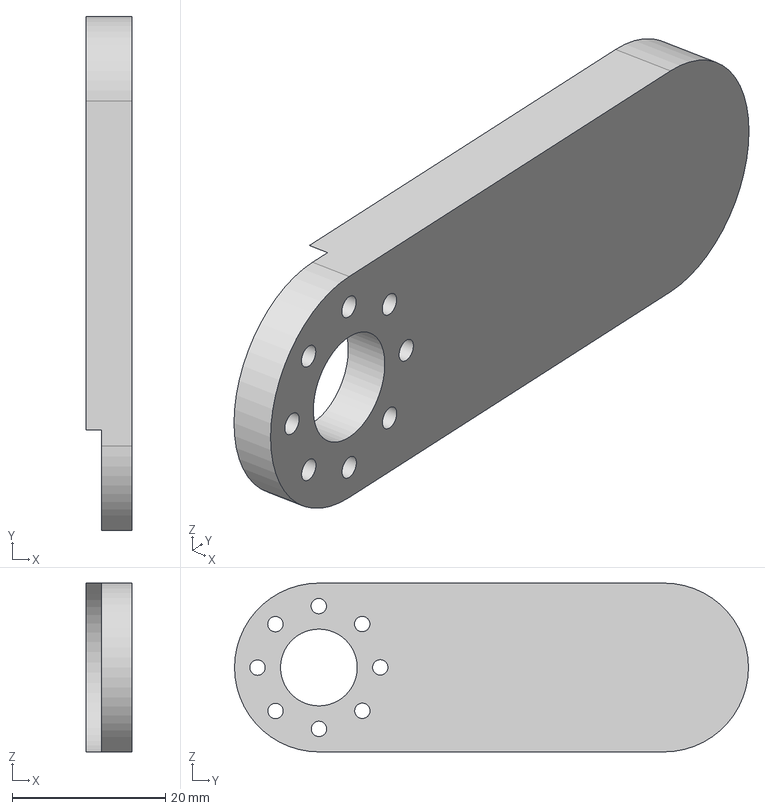
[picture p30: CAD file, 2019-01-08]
STEP Files/Release Lever v1.step
6.00 x 67.0 x 22.0 mm

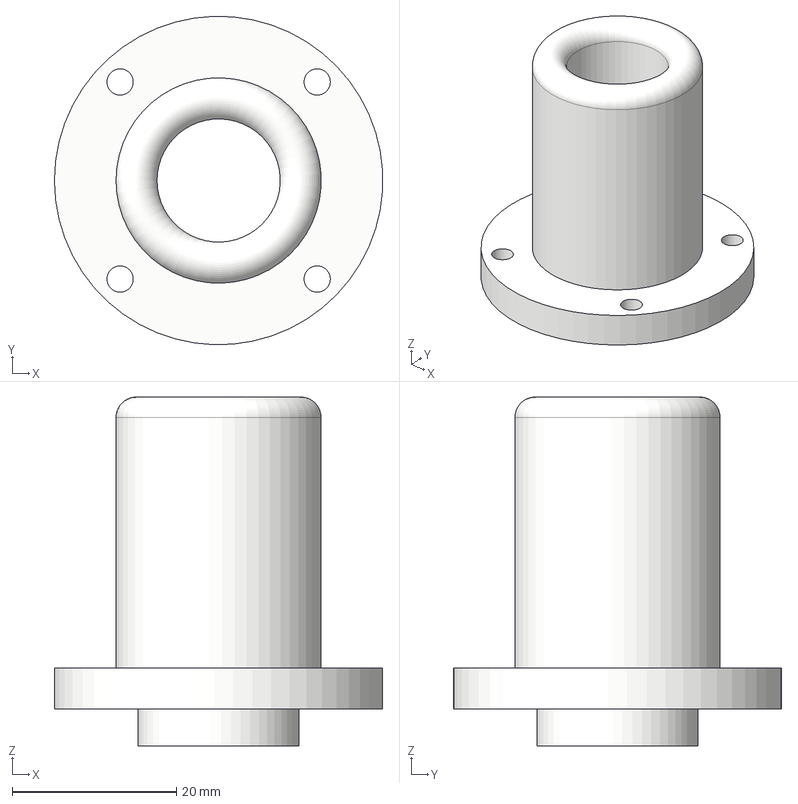
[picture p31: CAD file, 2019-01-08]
STEP Files/Outer Guide Tube v8.step
40.0 x 40.0 x 42.5 mm

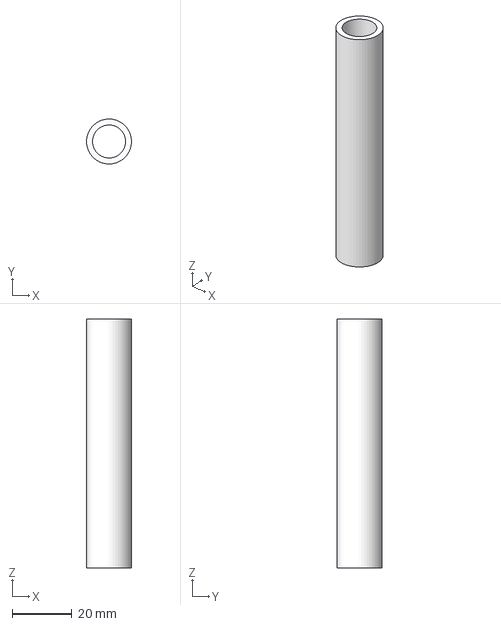
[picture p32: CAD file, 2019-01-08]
STEP Files/Axle v4.step
15.0 x 15.0 x 83.0 mm

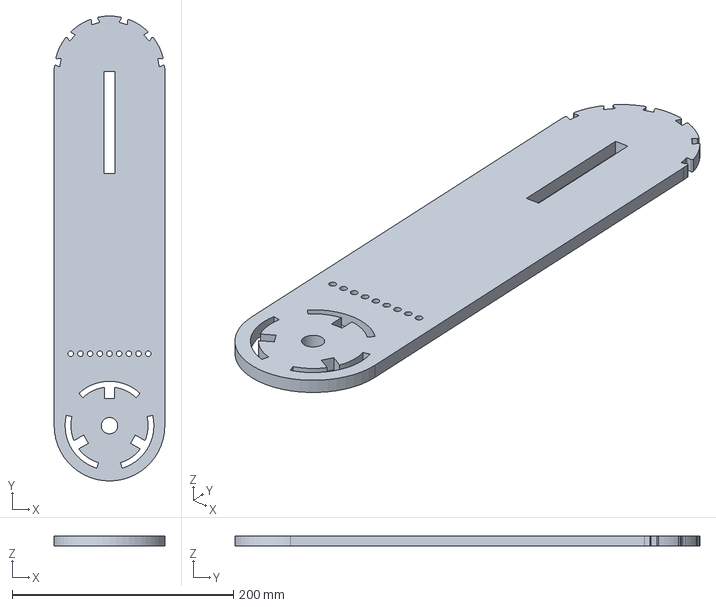
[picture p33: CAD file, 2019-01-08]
STEP Files/Leg v5.step
100.0 x 420.0 x 9.00 mm

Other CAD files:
STEP Files/Encoder Dynamixel Bracket v5.step
STEP Files/Front v13.step
STEP Files/PCB Representation v2.step
STEP Files/Runner v6.step
STEP Files/FootV2 v8.step
STEP Files/Guide Rail Representation v4.step
STEP Files/Inner Guide Tube v8.step
STEP Files/Motor Shaft Adapter v2.step
STEP Files/Pulleys v6.step
STEP Files/Rod Adapter v2.step
STEP Files/Runner Nut Representation v3.step
STEP Files/Runner Support v5.step
STEP Files/Threaded Rod Representation v2.step
STL Files/Acc Bracket v1.stl
STL Files/Axle v4.stl
STL Files/Dowel v11.stl
STL Files/Dynamixel RX28 Representation v1.stl
STL Files/FootV2 v8.stl
STL Files/Front v13.stl
STL Files/Guide Rail Representation v4.stl
STL Files/Inner Guide Tube v8.stl
STL Files/Leg v5.stl
STL Files/Motor Mount v5.stl
STL Files/Motor Shaft Adapter v2.stl
STL Files/Nylon to Flex Adapterv4.stl
STL Files/Outer Guide Tube v8.stl
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

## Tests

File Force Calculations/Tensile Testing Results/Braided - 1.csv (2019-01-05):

Time | Displacement | Force
(s) | (mm) | (kN)
0.0000 | 0.0000 | 0.0000
0.1000 | 0.1343 | 0.0004
0.2000 | 0.3161 | 0.0012
0.3000 | 0.4916 | 0.0020
0.4000 | 0.6637 | 0.0027
0.5000 | 0.8332 | 0.0034
0.6000 | 1.0015 | 0.0040
0.7000 | 1.1687 | 0.0046
0.8000 | 1.3363 | 0.0053
0.9000 | 1.5033 | 0.0059
1.0000 | 1.6699 | 0.0065
1.1000 | 1.8365 | 0.0070
1.2000 | 2.0035 | 0.0075
1.3000 | 2.1701 | 0.0080
1.4000 | 2.3368 | 0.0085
1.5000 | 2.5033 | 0.0091
1.6000 | 2.6701 | 0.0095
1.7000 | 2.8367 | 0.0099
1.8000 | 3.0032 | 0.0103
1.9000 | 3.1699 | 0.0107
2.0000 | 3.3367 | 0.0112
2.1000 | 3.5033 | 0.0115
2.2000 | 3.6700 | 0.0120
2.3000 | 3.8364 | 0.0124
2.4000 | 4.0033 | 0.0128
2.5000 | 4.1703 | 0.0131
2.6000 | 4.3367 | 0.0135
2.7000 | 4.5032 | 0.0139
2.8000 | 4.6703 | 0.0143
2.9000 | 4.8369 | 0.0146
3.0000 | 5.0033 | 0.0150
3.1000 | 5.1701 | 0.0153
3.2000 | 5.3368 | 0.0157
3.3000 | 5.5036 | 0.0160
3.4000 | 5.6701 | 0.0163
3.5000 | 5.8367 | 0.0166
3.6000 | 6.0035 | 0.0170
3.7000 | 6.1703 | 0.0173
3.8000 | 6.3367 | 0.0177
3.9000 | 6.5032 | 0.0179
4.0000 | 6.6701 | 0.0182
4.1000 | 6.8368 | 0.0185
4.2000 | 7.0032 | 0.0188
4.3000 | 7.1697 | 0.0191
4.4000 | 7.3368 | 0.0194
4.5000 | 7.5035 | 0.0196
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

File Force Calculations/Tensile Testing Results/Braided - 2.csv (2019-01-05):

Time | Displacement | Force
(s) | (mm) | (kN)
0.0000 | 0.0000 | -0.0005
0.1000 | 0.1343 | 0.0005
0.2000 | 0.3160 | 0.0022
0.3000 | 0.4917 | 0.0035
0.4000 | 0.6635 | 0.0045
0.5000 | 0.8332 | 0.0053
0.6000 | 1.0015 | 0.0060
0.7000 | 1.1688 | 0.0066
0.8000 | 1.3360 | 0.0071
0.9000 | 1.5032 | 0.0076
1.0000 | 1.6697 | 0.0080
1.1000 | 1.8363 | 0.0084
1.2000 | 2.0032 | 0.0087
1.3000 | 2.1701 | 0.0090
1.4000 | 2.3367 | 0.0092
1.5000 | 2.5029 | 0.0094
1.6000 | 2.6697 | 0.0096
1.7000 | 2.8367 | 0.0098
1.8000 | 3.0032 | 0.0099
1.9000 | 3.1697 | 0.0099
2.0000 | 3.3365 | 0.0099
2.1000 | 3.5033 | 0.0102
2.2000 | 3.6699 | 0.0104
2.3000 | 3.8364 | 0.0107
2.4000 | 4.0032 | 0.0110
2.5000 | 4.1701 | 0.0112
2.6000 | 4.3367 | 0.0113
2.7000 | 4.5029 | 0.0113
2.8000 | 4.6699 | 0.0114
2.9000 | 4.8368 | 0.0116
3.0000 | 5.0033 | 0.0118
3.1000 | 5.1699 | 0.0120
3.2000 | 5.3367 | 0.0123
3.3000 | 5.5035 | 0.0125
3.4000 | 5.6700 | 0.0127
3.5000 | 5.8365 | 0.0128
3.6000 | 6.0033 | 0.0130
3.7000 | 6.1701 | 0.0133
3.8000 | 6.3367 | 0.0134
3.9000 | 6.5032 | 0.0137
4.0000 | 6.6699 | 0.0139
4.1000 | 6.8367 | 0.0141
4.2000 | 7.0033 | 0.0143
4.3000 | 7.1696 | 0.0145
4.4000 | 7.3365 | 0.0147
4.5000 | 7.5033 | 0.0148
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

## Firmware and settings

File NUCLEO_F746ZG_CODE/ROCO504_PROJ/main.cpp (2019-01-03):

#include <list>
#include <vector>
#include "mbed.h"
#include "Dynamixel.h"
#include "MPU6050.h"
#include "motors.h"
#include "serial.h"

#define POST_SUCCESS    true
#define POST_FAIL       false

#define DebugLED1       PC_11
#define DebugLED2       PC_12
#define DebugLED3       PD_2

/*==
LEDS
==*/
DigitalOut redLED(DebugLED1);
DigitalOut yellowLED(DebugLED2);
DigitalOut greenLED(DebugLED3);

/*=======
FUNCTIONS
=======*/   
void    preTensioning();
float   getGyroValues();
bool    POST();
void    findServos();

/*==========================
PRE-TENSION/FALLING BOOLEANS
==========================*/
bool    taughtLeft = false;
bool    taughtRight = false;
bool    fallingLeft = false;
bool    fallingRight = false;

/*=
MPU
=*/
MPU6050 mpu;
float xAngle = 0;
float yAngle = 0;
float zAngle = 0;
float accel_x = 0;
float accel_y = 0;
float accel_z = 0;


/*==========
    MAIN    
==========*/
int main() {
    
    i2c.frequency(400000);          //use 400kHz I2C to MPU
    
    lMotorEN.period_ms(10);         //set motors' PWM period to 10ms
    rMotorEN.period_ms(10);
    
    bumperEnable = 1;                   //set bumper enable pin high
    lBumpTop.rise(&lMotorStop);         //attach left bumper top rising edge interrupt to left motor stop function
    lBumpBottom.rise(&lMotorStop);      //attach left bumper bottom rising edge interrupt to left motor stop function
    rBumpTop.rise(&rMotorStop);         //attach right bumper top rising edge interrupt to right motor stop function
    rBumpBottom.rise(&rMotorStop);      //attach right bumper bottom rising edge interrupt to right motor stop function
    lBumpTop.fall(&lMotorReleased);     //attach left bumper top falling edge interrupt to left motor released function
    lBumpBottom.fall(&lMotorReleased);  //attach left bumper bottom falling edge interrupt to left motor released function
    rBumpTop.fall(&rMotorReleased);     //attach right bumper top falling edge interrupt to right motor released function
    rBumpBottom.fall(&rMotorReleased);  //attach right bumper bottom falling edge interrupt to right motor released function
        
    
    lMotorBumped = false;
    rMotorBumped = false;
    
    //try and move right motor up for 1 second.
    //this is useful if the motor is stuck at the bottom..
    //..when robot is turned on
    rMotorUp(1.0f);
    motorTimeout.attach(&motorStop, 1.0);
       
    
    /*==
    POST
    ==*/
    //(power on self test)
    bool POST_result = POST();

    if(POST_result == POST_FAIL){
        //quit program as POST has failed
        PCSERIAL("*********************\n");
        PCSERIAL("POST FAILED - EXITING\n");
        PCSERIAL("*********************\n");
        yellowLED = 1;
        exit(EXIT_FAILURE);
    }
    
    /*======================
    Dynamixel Class Creation
    ======================*/
    //create two instances of the Dynamixel class based on the two servo..
    //..ID's found in POST
    Dynamixel RX28_1(DynamixelTX, DynamixelRX, txEnable, ServoID[0], DynamixelBaud);
    Dynamixel RX28_2(DynamixelTX, DynamixelRX, txEnable, ServoID[1], DynamixelBaud);
    
    
    /*=================
    TOGGLING SERVO LEDS
    =================*/
    for(uint8_t i = 0; i < 3; i++){
        PCSERIAL("TOGGLING SERVO 1\n");
        RX28_1.toggleLED(0);
        wait_ms(75);
        RX28_1.toggleLED(1);
        wait_ms(75);
    }
    for(uint8_t i = 0; i < 3; i++){
        PCSERIAL("TOGGLING SERVO 2\n");
        RX28_2.toggleLED(0);
        wait_ms(75);
        RX28_2.toggleLED(1);
        wait_ms(75);
    }
    
    /*=============
    TURN OFF TORQUE
    =============*/
    RX28_1.torqueToggle(TORQUE_DISABLE);
    
    deltat = 0.01875;
    
    //need this delay as the status packet from RX28_1 torque toggle is.. 
    //..on the line so have to wait for that to finish
    wait_ms(1);
    
    /*===================
    RESET LEG RELEASE PIN
    ===================*/
    //move leg release pin back into locking position
    RX28_2.move(512);
    
    PCSERIAL("Starting up MPU\n");
    
    //allow gyro to start up and empty its FIFO
    for(int i = 0; i < 1024; i++){
        getGyroValues();
    }
    
    PCSERIAL("**************************************\n\n");
    PCSERIAL("ROBOT MUST BE VERTICAL DURING START-UP\n\n");
    PCSERIAL("**************************************\n\n");
    
    //wait for robot to be lifted up
    while(yAngle > 2 || yAngle < -2){
        getGyroValues();
        redLED = 1;
    }
    
    PCSERIAL("Robot Vertical\n\r");
    
    //allow robot to be steadied so doesn't detect a fall straight away
    wait_ms(1000);
    
    PCSERIAL("Calibratiing Right Motor\n\r");
    
    //try and calibrate right motor by moving it all the way to the bottom..
    //..and then bringing it back up slightly
    rMotorDown(0.5f);
    while(1){
       if(!rMotorBumped){
           yellowLED = 1;  
       }else{
           yellowLED = 0;
           wait_ms(500);
           rMotorUp(1.0f);
           motorTimeout.attach(&motorStop, 4.0f);
           break;
       }
    }
    
    wait_ms(5000);
    
    PCSERIAL("Right Motor Calibrated\n\r");      
    
    while(1){
        //vector to hold 50 values of acceleration in x axis
        std::vector<float> gyroVals;
        float accel_average = 0;
        float cummulative_accel = 0;
        
        taughtLeft = false;
        taughtRight = false;
        fallingLeft = false;
        fallingRight = false;
    
        redLED = 0;
        greenLED = 1;
        
        //remember the position of the leg before it falls
        uint16_t originalLegPos = RX28_1.getPosition();

        uint16_t newLegPos = originalLegPos;
        
        //pre-tension the leg based on which way it is being tipped
        preTensioning();
        
        //falling so turn on red LED
        redLED = 1;
        greenLED = 0;
        
        PCSERIAL("LEG FALLING\n");
        
        
        //deploy leg to right
        if(fallingRight == true){
            
            //pull up left motor to swing leg round
            lMotorUp(1.0f);
            //stop motor after 5 seconds
            motorTimeout.attach(&motorStop, 5.0f);
            //release leg pin
            RX28_2.move(700);
            
            //stay in loop unless acceleration of body has stabalised
            while(1){
                //measure the acceleration in x axis 50 times and save into vector
                for(int n=0; n<50; n++){
                    gyroVals.push_back(getGyroValues());
                    cummulative_accel = cummulative_accel + accel_x;
                    wait_ms(3);
                }
                
                //calculate average acceleration over the 50 samples
                accel_average = (cummulative_accel)/50;
                
                PCSERIAL("%f\n", accel_average);
                
                //if acceleration has stabalised to over 0.5 then we know body..
                //..has steadied. Refer to MATLAB graphs as to why we use 0.5..
                //..and not 0
                if(accel_average > 0.5f){
                    lMotorDown(0.4);        //start moving left motor down slowly
                    break;                  //break out of while loop
                }else{
                    gyroVals.clear();       //reset vector
                    cummulative_accel = 0;  //reset cummulative acceleration value
                }
            }
            
            //get position of the leg
            newLegPos = RX28_1.getPosition();
            
            //stay in loop until leg is within 20 degrees of being perpendicular..
            //..to the body. 3.4 units = 1 degree. While this is happening the left..
            //..motor is still moving down, or trying to.
            while(abs(newLegPos-originalLegPos)>68){
                newLegPos = RX28_1.getPosition();
                PCSERIAL("%d\n", newLegPos);
            }
            
            //stop motor once body is relatively flat
            motorTimeout.attach(&motorStop, 0.0);

            //turn on finished LED
            greenLED = 1;
            
        //deploy leg to left
        }else if(fallingLeft == true){ 
        
            //pull up right motor to swing leg round
            rMotorUp(1.0f);
            //stop motor after 5 seconds
            motorTimeout.attach(&motorStop, 5.0f);
            //release leg pin
            RX28_2.move(700);
            
            //stay in loop unless acceleration of body has stabalised
            while(1){
                //measure the acceleration in x axis 50 times and save into vector
                for(int n=0; n<50; n++){
                    gyroVals.push_back(getGyroValues());
                    cummulative_accel = cummulative_accel + accel_x;
                    wait_ms(3);
                }
                
                //calculate average acceleration over the 50 samples
                accel_average = (cummulative_accel)/50;
                
                PCSERIAL("%f\n", accel_average);
                
                //if acceleration has stabalised to over 0.5 then we know body..
                //..has steadied. Refer to MATLAB graphs as to why we use 0.5..
                //..and not 0
                if(accel_average > 0.5f){
                    rMotorDown(0.4);        //start moving right motor down slowly
                    break;                  //break out of while loop
                }else{
                    gyroVals.clear();       //reset vector
                    cummulative_accel = 0;  //reset cummulative acceleration value
                }
            }
            
            //get position of the leg
            newLegPos = RX28_1.getPosition();
            
            //stay in loop until leg is within 20 degrees of being perpendicular..
            //..to the body. 3.4 units = 1 degree. While this is happening the right..
            //..motor is still moving down, or trying to.
            while(abs(newLegPos-originalLegPos)>50){
                newLegPos = RX28_1.getPosition();
                PCSERIAL("%d\n", newLegPos);
            }
            
            //stop motor once body is relatively flat
            motorTimeout.attach(&motorStop, 0.0);

            //turn on finished LED
            greenLED = 1;
        
        }
        
        //exist with successful execution  
        exit(EXIT_SUCCESS);
    }
      
}
/*==============
    END MAIN    
==============*/





/*===================
    getGyroValues            
===================*/
float getGyroValues(){
    // check to see if 'data ready' bit set
    if(mpu.readByte(MPU6050_ADDRESS, INT_STATUS) & 0x01) {
        //read accleration data
        mpu.readAccelData(accelCount);
        mpu.getAres();
        
        //calculate the accleration value into actual g's
        ax = (float)accelCount[0]*aRes - accelBias[0];  //get actual g value, this depends on scale being set
        ay = (float)accelCount[1]*aRes - accelBias[1];
        az = (float)accelCount[2]*aRes - accelBias[2];
        
        //read gyro data
        mpu.readGyroData(gyroCount);
        mpu.getGres();
        
        //calculate the gyro value into actual degrees per second
        gx = (float)gyroCount[0]*gRes;      //get actual gyro value, this depends on scale being set
        gy = (float)gyroCount[1]*gRes;
        gz = (float)gyroCount[2]*gRes;

    }
    
    //pass gyro rate as rad/s
    mpu.MadgwickQuaternionUpdate(ax, ay, az, gx*PI/180.0f, gy*PI/180.0f, gz*PI/180.0f);
    
    //convert Quaternions to Euler angles
    yaw   = atan2(2.0f * (q[1] * q[2] + q[0] * q[3]), q[0] * q[0] + q[1] * q[1] - q[2] * q[2] - q[3] * q[3]);   
    pitch = -asin(2.0f * (q[1] * q[3] - q[0] * q[2]));
    roll  = atan2(2.0f * (q[0] * q[1] + q[2] * q[3]), q[0] * q[0] - q[1] * q[1] - q[2] * q[2] + q[3] * q[3]);
    pitch *= 180.0f / PI;
    yaw   *= 180.0f / PI; 
    roll  *= 180.0f / PI;
    
    xAngle = roll;
    yAngle = pitch;
    zAngle = yaw;
    
    accel_x = ax;
    accel_y = ay;
    accel_z = az;
    
    return accel_x;

}


/*===================
    preTensioning            
===================*/
void preTensioning(){
            
    //pre-tensioning while robot is standing.
    //any more than 10 degrees tilt is a 'fall'
    while(yAngle > -10 & yAngle < 10){
        
        getGyroValues();
        
        //booleans are used to make sure each if statement is only executed once
        
        //falling right if looking at robot from front
        if(yAngle >= 4 && taughtLeft == false){
            //tension left, release right
            //lMotorUp(1.0f);
            rMotorDown(0.7f);
            //move motors for 2 seconds
            motorTimeout.attach(&motorStop, 2.0);
            taughtLeft = true;
            taughtRight = false;
            fallingRight = true;
            fallingLeft = false;
        }
        
        //falling left if looking at robot from front
        if(yAngle <= -4 && taughtRight == false){
            //tension right, release left
            //lMotorDown(1.0f);
            rMotorUp(1.0f);
            //move motors for 2 seconds
            motorTimeout.attach(&motorStop, 2.0);
            taughtLeft = false;
            taughtRight = true;
            fallingRight = false;
            fallingLeft = true;
        }
    }
    
}


/*==========
    POST    
==========*/
bool POST() {
 
    bool _POST_result;
    
    //toggle LEDs
    redLED = 0;
    yellowLED = 0;
    greenLED = 0;
    wait_ms(200);
    redLED = 1;
    wait_ms(200);
    yellowLED = 1;
    wait_ms(200);
    greenLED = 1;
    wait_ms(200);
    redLED = 0;
    yellowLED = 0;
    greenLED = 0;
    wait_ms(200);
        
    //find which Dynamixel servos are in the chain
    findServos();
    
    //print found servo ID numbers
    for(char i = 0; i < NumberOfServos; i++){
        PCSERIAL("SERVO ID = %d\n", ServoID[i]);
    }
        
    //create two instances of Dynamixel classes with the found servos
    Dynamixel _RX28_1(DynamixelTX, DynamixelRX, txEnable, ServoID[0], DynamixelBaud);
    Dynamixel _RX28_2(DynamixelTX, DynamixelRX, txEnable, ServoID[1], DynamixelBaud);

    //try to ping the servos and record the error (if there is one)
    uint8_t RX28_1_Error = _RX28_1.ping();
    uint8_t RX28_2_Error = _RX28_2.ping();
    
    if(RX28_1_Error==0&&RX28_2_Error==0){
        //No errors
        PCSERIAL("\n============================\n");
        PCSERIAL("ALL SERVOS PINGED. NO ERRORS\n");
        PCSERIAL("============================\n");
        _POST_result = POST_SUCCESS; 
    }else{ 
        PCSERIAL("\n******************\n");
        PCSERIAL("SERVO ERRORS FOUND\n");
        PCSERIAL("******************\n");
        _POST_result = POST_FAIL;
    }
    
    if(RX28_1_Error == 128){
        PCSERIAL("******************\n");
        PCSERIAL("RX28_1 UNREACHABLE\n");
        PCSERIAL("******************\n");        
    }else if(RX28_1_Error != 0){
        PCSERIAL("*******************\n");
        PCSERIAL("RX28_1 ERROR = %x\n", RX28_1_Error);
        PCSERIAL("*******************\n");
    }
    if(RX28_2_Error == 128){
        PCSERIAL("******************\n");
        PCSERIAL("RX28_2 UNREACHABLE\n");
        PCSERIAL("******************\n");        
    }else if(RX28_2_Error != 0){
        PCSERIAL("*******************\n");
        PCSERIAL("RX28_2 ERROR = %x\n", RX28_2_Error);
        PCSERIAL("*******************\n");
    }
    
    
    //read 'who am I' register to test communication with MPU
    uint8_t whoami = mpu.readByte(MPU6050_ADDRESS, WHO_AM_I_MPU6050);
    PCSERIAL("TESTING COMMS\n");
    PCSERIAL("MPU ID = %x\n", whoami);
    
    //whoami should be equal to 0x68 which is hard-coded into the MPU
    if(whoami != 0x68) {
        PCSERIAL("MPU COMMS FAIL OR ID INCORRECT - EXITING\n");
        exit(EXIT_FAILURE);
    }
    
    PCSERIAL("MPU6050 ONLINE\n");
    
    //test the MPU
    mpu.MPU6050SelfTest(SelfTest);
    
    //if tests have returned values within the correct ranges then begin 
    //..setting up MPU
    if(SelfTest[0] < 1.0f && SelfTest[1] < 1.0f && SelfTest[2] < 1.0f && SelfTest[3] < 1.0f && SelfTest[4] < 1.0f && SelfTest[5] < 1.0f) {
        mpu.resetMPU6050();                         //reset
        mpu.calibrateMPU6050(gyroBias, accelBias);  //calibrate
        mpu.initMPU6050();                          //initialise
        PCSERIAL("MPU INITIALISED\n");
    } else {
        PCSERIAL("MPU FAILED TO PASS SELF-TEST\n");
    }
    
    //return result back to main
    return _POST_result;
    
}


/*================
    findServos      
================*/
void findServos(){
    
    yellowLED = 1;
    
    /*=========================================================================
    THE FOLLOWING BLOCK OF CODE WAS USED TO TRY AND SET ALL BAUD RATES OF 
    SERVOS IN THE CHAIN TO 57600. THIS WAS DONE AS THE BAUD RATES OF THE SERVOS
    WERE NOT NECCESSARILY THE SAME TO BEGIN WITH.
    =========================================================================*/
    /*
    static const int baudRatesArr[] = {9600, 19200, 57600, 115200, 200000, 250000, 400000, 500000, 1000000};
    vector<int> baudRates (baudRatesArr, baudRatesArr + sizeof(baudRatesArr) / sizeof(baudRatesArr[0]));
    
    //loop through all possibilites of baud rates as baud rates of the servos..
    //..in the chain are unknown
    for(int i=0; i<9; i++){
        //Using broadcast ID so only need to send once
        Dynamixel RX28_x(DynamixelTX, DynamixelRX, txEnable, BROADCAST_ID, baudRateArr[i]);
        PCSERIAL("\nTrying to set baud rate to 57600 for all servos at baudrate %d\n", baudRateArr[i]);
        uint8_t RX28_x_Res = RX28_x.setBaud();          //set baud rate
    }
    */
    
    Dynamixel RX28_x(DynamixelTX, DynamixelRX, txEnable, BROADCAST_ID, DynamixelBaud);
    RX28_x.setReturnDelay();    // set return delay to 256*2uS
    
    wait_ms(1000);
    
    char ServosFound = 0;       
    
    for(uint8_t i = 1; i < 253; i++){
        
        // redeclared Dynamixel object with changing servo ID
        Dynamixel RX28_x(DynamixelTX, DynamixelRX, txEnable, i, DynamixelBaud);
        uint8_t RX28_x_Res = RX28_x.findServo();        //try and find servo in chain with that ID
        
        //check servo error returned
        if(RX28_x_Res == 0xff){
            PCSERIAL("SERVO ID %d UNREACHABLE\n", i);
        }else if(RX28_x_Res != 0xff){
            PCSERIAL("SERVO ID %d FOUND\n", i);
          
            switch (ServosFound) {
                case 0:
                    ServoID[0] = i;
                    break;
                case 1:
                    ServoID[1] = i;
                    break;
                default:
                    PCSERIAL("TOO MANY SERVOS FOUND\n");
            }
            ServosFound += 1;
        }
        
        if(ServosFound == NumberOfServos){
            PCSERIAL("\n================\n");
            PCSERIAL("ALL SERVOS FOUND\n");
            PCSERIAL("================\n");
            wait_ms(200);
            break;
        }
        
    }
    
    yellowLED = 0;
    
}

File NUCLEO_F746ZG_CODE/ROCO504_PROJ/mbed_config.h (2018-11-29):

/*
 * mbed SDK
 * Copyright (c) 2017 ARM Limited
 *
 * Licensed under the Apache License, Version 2.0 (the "License");
 * you may not use this file except in compliance with the License.
 * You may obtain a copy of the License at
 *
 * http://www.apache.org/licenses/LICENSE-2.0
 *
 * Unless required by applicable law or agreed to in writing, software
 * distributed under the License is distributed on an "AS IS" BASIS,
 * WITHOUT WARRANTIES OR CONDITIONS OF ANY KIND, either express or implied.
 * See the License for the specific language governing permissions and
 * limitations under the License.
 */

// Automatically generated configuration file.
// DO NOT EDIT, content will be overwritten.

#ifndef __MBED_CONFIG_DATA__
#define __MBED_CONFIG_DATA__

// Configuration parameters
#define CLOCK_SOURCE                                                          USE_PLL_HSE_EXTC|USE_PLL_HSI                                                                     // set by target:NUCLEO_F746ZG
#define LPTICKER_DELAY_TICKS                                                  1                                                                                                // set by target:FAMILY_STM32
#define MBED_CONF_ATMEL_RF_ASSUME_SPACED_SPI                                  1                                                                                                // set by library:atmel-rf[STM]
#define MBED_CONF_ATMEL_RF_FULL_SPI_SPEED                                     7500000                                                                                          // set by library:atmel-rf
#define MBED_CONF_ATMEL_RF_FULL_SPI_SPEED_BYTE_SPACING                        250                                                                                              // set by library:atmel-rf
#define MBED_CONF_ATMEL_RF_LOW_SPI_SPEED                                      3750000                                                                                          // set by library:atmel-rf
#define MBED_CONF_ATMEL_RF_PROVIDE_DEFAULT                                    0                                                                                                // set by library:atmel-rf
#define MBED_CONF_ATMEL_RF_USE_SPI_SPACING_API                                0                                                                                                // set by library:atmel-rf
#define MBED_CONF_CELLULAR_DEBUG_AT                                           0                                                                                                // set by library:cellular
#define MBED_CONF_CELLULAR_RANDOM_MAX_START_DELAY                             0                                                                                                // set by library:cellular
#define MBED_CONF_CELLULAR_USE_APN_LOOKUP                                     1                                                                                                // set by library:cellular
#define MBED_CONF_DRIVERS_UART_SERIAL_RXBUF_SIZE                              256                                                                                              // set by library:drivers
#define MBED_CONF_DRIVERS_UART_SERIAL_TXBUF_SIZE                              256                                                                                              // set by library:drivers
#define MBED_CONF_ESP8266_DEBUG                                               0                                                                                                // set by library:esp8266
#define MBED_CONF_ESP8266_PROVIDE_DEFAULT                                     0                                                                                                // set by library:esp8266
#define MBED_CONF_EVENTS_PRESENT                                              1                                                                                                // set by library:events
#define MBED_CONF_EVENTS_SHARED_DISPATCH_FROM_APPLICATION                     0                                                                                                // set by library:events
#define MBED_CONF_EVENTS_SHARED_EVENTSIZE                                     256                                                                                              // set by library:events
#define MBED_CONF_EVENTS_SHARED_HIGHPRIO_EVENTSIZE                            256                                                                                              // set by library:events
#define MBED_CONF_EVENTS_SHARED_HIGHPRIO_STACKSIZE                            1024                                                                                             // set by library:events
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

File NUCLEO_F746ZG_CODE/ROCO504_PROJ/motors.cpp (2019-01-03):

#include "mbed.h"
#include "motors.h"

#define lMotorIN1Pin    PG_0
#define lMotorIN2Pin    PD_1
#define rMotorIN3Pin    PD_0
#define rMotorIN4Pin    PF_8
#define lMotorENPin     PF_9
#define rMotorENPin     PF_7
#define lBumpTopPin     PF_12   //purple
#define lBumpBottomPin  PD_14   //yellow
#define rBumpTopPin     PA_7    //green
#define rBumpBottomPin  PD_15   //blue

/*==============
DC MOTOR CONTROL
==============*/
DigitalOut  lMotorIN1(lMotorIN1Pin);
DigitalOut  lMotorIN2(lMotorIN2Pin);
PwmOut      lMotorEN(lMotorENPin);

DigitalOut  rMotorIN3(rMotorIN3Pin);
DigitalOut  rMotorIN4(rMotorIN4Pin);
PwmOut      rMotorEN(rMotorENPin);

/*======
TIMEOUTS
======*/
Timeout     motorTimeout;
Timeout     lMotorTimeout;
Timeout     rMotorTimeout;
Timeout     lMotorISREnable;
Timeout     rMotorISREnable;

/*========
INTERRUPTS
========*/
InterruptIn lBumpTop(lBumpTopPin);
InterruptIn lBumpBottom(lBumpBottomPin);
InterruptIn rBumpTop(rBumpTopPin);
InterruptIn rBumpBottom(rBumpBottomPin);

/*==============
POWER TO BUMPERS
==============*/
DigitalOut  bumperEnable(PC_6);

volatile bool lMotorBumped;
volatile bool rMotorBumped;

/*========================
MOTOR AND BUMPER FUNCTIONS
========================*/
//function to enable left bumpers
void lMotorBumperEnable(){
    lBumpTop.rise(&lMotorStop);
    lBumpBottom.rise(&lMotorStop);
    lBumpTop.fall(&lMotorReleased);
    lBumpBottom.fall(&lMotorReleased);
}

//function to enable right bumpers
void rMotorBumperEnable(){
    rBumpTop.rise(&rMotorStop);
    rBumpBottom.rise(&rMotorStop);
    rBumpTop.fall(&rMotorReleased);
    rBumpBottom.fall(&rMotorReleased);
}

//function to stop both motors
void motorStop(){
    lMotorEN.write(0.0f);
    rMotorEN.write(0.0f);
}

//function to stop left motor and try and get rid of switch debounce by..
//..disabling interrupts and then attach interrupts again after 100ms
void lMotorStop(){
    lBumpTop.rise(NULL);
    lBumpBottom.rise(NULL);
    lBumpTop.fall(NULL);
    lBumpBottom.fall(NULL);
    lMotorEN.write(0.0f);
    lMotorBumped = true;
    lMotorISREnable.attach(&lMotorBumperEnable, 0.10f);
}

//function to stop right motor and try and get rid of switch debounce by..
//..disabling interrupts and then attach interrupts again after 100ms
void rMotorStop(){
    rBumpTop.rise(NULL);
    rBumpBottom.rise(NULL);
    rBumpTop.fall(NULL);
    rBumpBottom.fall(NULL);
    rMotorEN.write(0.0f);
    rMotorBumped = true;
    rMotorISREnable.attach(&rMotorBumperEnable, 0.10f);
}

//function to move left motor up at set speed (0-1) where 1 is full power
void lMotorUp(float speed){
    lMotorIN1 = 1;
    lMotorIN2 = 0;
    lMotorEN.write(speed);
}

//function to move left motor down at set speed (0-1) where 1 is full power
void lMotorDown(float speed){
    lMotorIN1 = 0;
    lMotorIN2 = 1;
    lMotorEN.write(speed);
}

//function to move right motor up at set speed (0-1) where 1 is full power
void rMotorUp(float speed){
    rMotorIN3 = 0;
    rMotorIN4 = 1;
    rMotorEN.write(speed);
}

//function to move right motor down at set speed (0-1) where 1 is full power
void rMotorDown(float speed){
    rMotorIN3 = 1;
    rMotorIN4 = 0;
    rMotorEN.write(speed);
}

//function for when left motor releases off a bumper
void lMotorReleased(){
    lMotorBumped = false;
    lBumpTop.rise(NULL);
    lBumpBottom.rise(NULL);
    lBumpTop.fall(NULL);
    lBumpBottom.fall(NULL);
    lMotorISREnable.attach(&lMotorBumperEnable, 0.10f);
}

//function for when right motor releases off a bumper
void rMotorReleased(){
    rMotorBumped = false;
    rBumpTop.rise(NULL);
    rBumpBottom.rise(NULL);
    rBumpTop.fall(NULL);
    rBumpBottom.fall(NULL);
    rMotorISREnable.attach(&rMotorBumperEnable, 0.10f);
}

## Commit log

2018-11-29 Initial upload of main.cpp and libraries.
    Does not include mbed-os folder, as it is too large at 1997 files. Code does need mbed-os folder to work. Dynamixel.cpp has been modified heavily to make sure the timings are correct with the RX28 servos.
    [Dynamixel.cpp, main.cpp, mbed_config.h]
2018-12-12 Updating main.cpp and creation of motors.cpp
    Robot is now fully built so proper testing can be done. This means properly sorting the DC motor code. Micro-switches have been attached so software knows when the motors are at their limits to prevent damage.
    Motor code has been updated to use timeouts as oppose to tickers. All code has been put in its own .cpp file with proper functions to control the motors.
    [main.cpp, motors.cpp]
2019-01-03 Main.cpp includes testing motors and gyro values
2019-01-03 Update main.cpp
    Code has been designed so can only fall one way depending on which motor is connected to tendons. Would need to be further modified for use of both motors working together as agonist/antagonist joint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
2019-01-05 Add files via upload
    Added Force Calculations and Tensile Testing Results.
    [Braided - 1.csv, Braided - 2.csv, Braided Nylon - 1.csv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]
2019-01-05 Added STL Files for all components
    [Acc Bracket v1.stl, Axle v4.stl, Bottom Dynamixel Bracket v5.stl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]
2019-01-08 Add files via upload
    MATLAB results using lower variable limits.
    [TorqueCalculations_LowerVariableLimits.csv]
2019-01-08 Create STL Files
2019-01-08 Added STL Files
    Re-uploaded with new folder name as old folder name was spelt "STL FIles" not "STL Files"
    [Acc Bracket v1.stl, Axle v4.stl, Bottom Dynamixel Bracket v5.stl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]
2019-01-08 Delete Acc Bracket v1.stl
    Folder name spelt incorrectly. "STL FIles" not "STL Files"
    [Acc Bracket v1.stl]
2019-01-08 Delete Bearing v3.stl
    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
2019-01-08 Delete Bottom Dynamixel Bracket v5.stl
    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
    [Bottom Dynamixel Bracket v5.stl]
2019-01-08 Delete Dowel v11.stl
    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
    [Dowel v11.stl]
2019-01-08 Delete Dynamixel RX28 Representation v1.stl
    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
    [Dynamixel RX28 Representation v1.stl]
2019-01-08 Delete FootV2 v8.stl
    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
    [FootV2 v8.stl]
2019-01-08 Delete Front v13.stl
    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
    [Front v13.stl]
2019-01-08 Delete Guide Rail Representation v4.stl
    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
    [Guide Rail Representation v4.stl]
2019-01-08 Delete Inner Guide Tube v8.stl
    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
    [Inner Guide Tube v8.stl]
2019-01-08 Delete Leg v5.stl
    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
    [Leg v5.stl]
2019-01-08 Delete Motor Mount v5.stl
    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
    [Motor Mount v5.stl]
2019-01-08 Delete Motor Shaft Adapter v2.stl
    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
    [Motor Shaft Adapter v2.stl]
2019-01-08 Delete Nylon to Flex Adapterv4.stl
    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
    [Nylon to Flex Adapterv4.stl]
2019-01-08 Delete Outer Guide Tube v8.stl
    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
    [Outer Guide Tube v8.stl]
2019-01-08 Delete PCB Representation v2.stl
    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
    [PCB Representation v2.stl]
2019-01-08 Delete Pulleys v6.stl
    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
    [Pulleys v6.stl]
2019-01-08 Delete Release Lever v1.stl
    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
    [Release Lever v1.stl]
2019-01-08 Delete Rod Adapter v2.stl
    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
    [Rod Adapter v2.stl]
2019-01-08 Delete Runner End v5.stl
    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
    [Runner End v5.stl]
2019-01-08 Delete Runner Nut Representation v3.stl
    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
    [Runner Nut Representation v3.stl]
2019-01-08 Delete Runner Support v5.stl
    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
    [Runner Support v5.stl]
2019-01-08 Delete Runner v6.stl
    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
    [Runner v6.stl]
2019-01-08 Delete Spine v6.stl
    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
    [Spine v6.stl]
2019-01-08 Delete Threaded Rod Representation v2.stl
    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
    [Threaded Rod Representation v2.stl]
2019-01-08 Delete Top Dynamixel Bracket v4.stl
    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
    [Top Dynamixel Bracket v4.stl]
2019-01-08 Added .step files for all 3D parts.
    Was recommended by Sam White to upload this file format for all 3D models/parts.
    [Acc Bracket v1.step, Axle v4.step, Bearing v3.step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]
